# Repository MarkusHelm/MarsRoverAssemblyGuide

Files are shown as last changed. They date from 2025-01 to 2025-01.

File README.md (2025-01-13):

# Mechanical

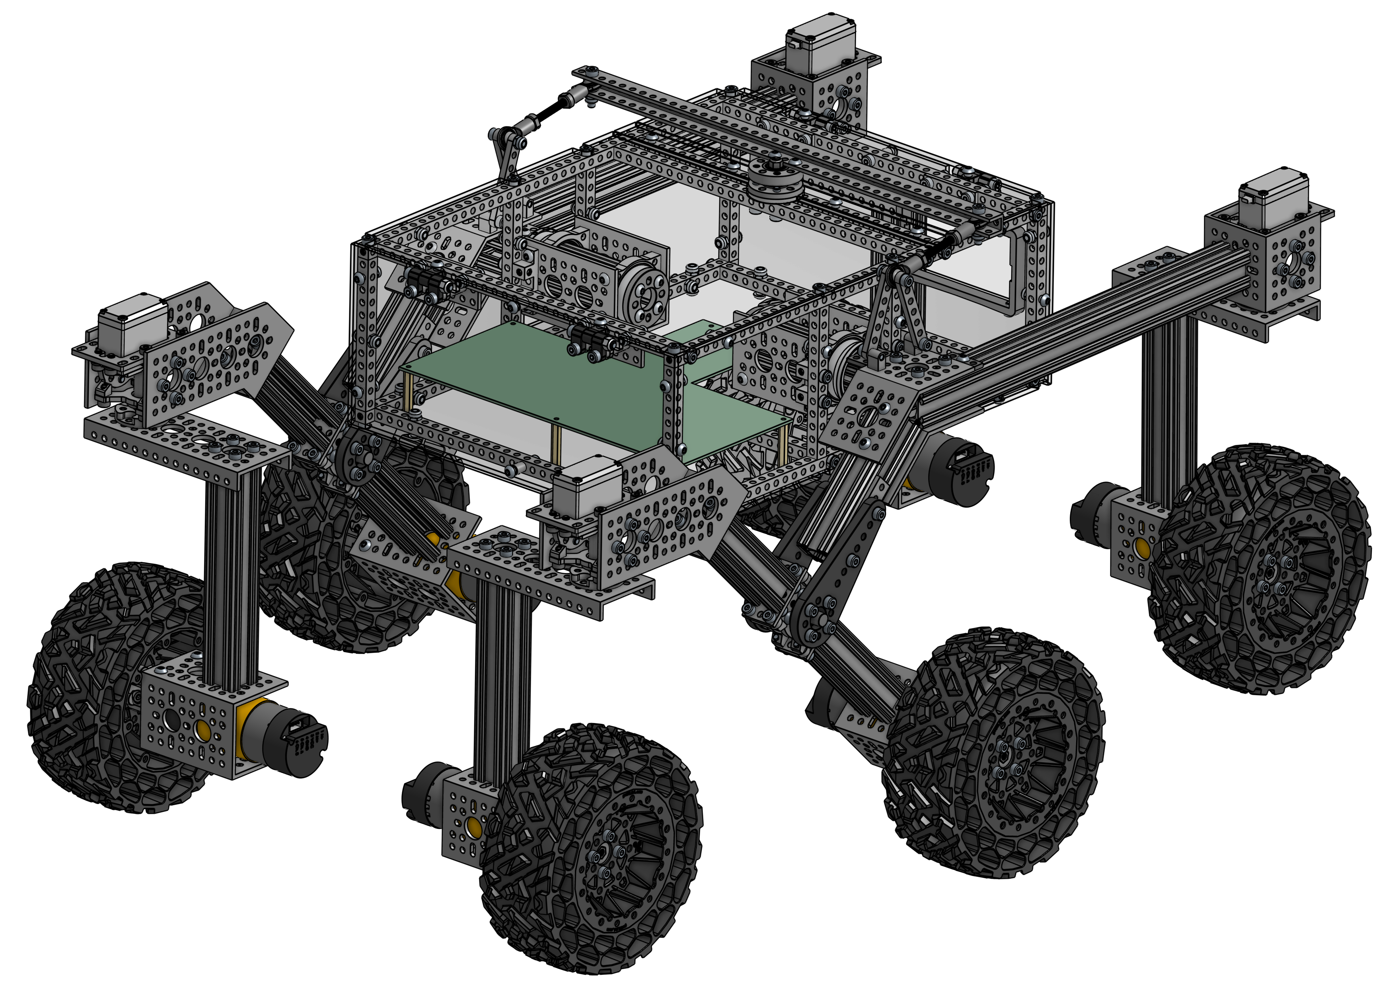
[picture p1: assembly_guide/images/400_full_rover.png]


## Assembly Guide

👉 [`Mechanical Assembly Guide`](./assembly_guide/readme.md)

## Required Parts

This is a summary of all the mechanical parts you need to build the rover. The amount is always the number of the `individual parts`. Some parts are sold in `(packs)`. The number in brackets indicates, how many packs you need.

> ⚠️ Be very careful when ordering the parts! Many parts have multiple variants, some with very small differences. It is important that you get the exact parts listed!

#### goBILDA Parts

| Amount | Part | Part Number | Link | Chapter |
| :----: | --- | --- | --- | --- |
| 1 | 1101 Series U-Beam (**41 Hole**, 328mm Length) | 1101-0041-0328 | https://www.gobilda.com/1101-series-u-beam-41-hole-328mm-length/ | Main Body |
| 8 (4)  | 1102 Series Flat Beam (**3 Hole**, 24mm Length) - 2 Pack | 1102-0003-0024 | https://www.gobilda.com/1102-series-flat-beam-3-hole-24mm-length-2-pack/ | Rocker Bogie |
| 4 (2)  | 1102 Series Flat Beam (**7 Hole**, 56mm Length) - 2 Pack | 1102-0007-0056 | https://www.gobilda.com/1102-series-flat-beam-7-hole-56mm-length-2-pack/ | Rocker Bogie |
| 8 | 1106 Series Square Beam (**12 Hole**, 96mm Length) | 1106-0012-0096 | https://www.gobilda.com/1106-series-square-beam-12-hole-96mm-length/ | Main Body |
| 7 | 1106 Series Square Beam (**29 Hole**, 232mm Length) | 1106-0029-0232 | https://www.gobilda.com/1106-series-square-beam-29-hole-232mm-length/ | Main Body |
| 4 | 1106 Series Square Beam (**41 Hole**, 328mm Length) | 1106-0041-0328 | https://www.gobilda.com/1106-series-square-beam-41-hole-328mm-length/ | Main Body |
| 4 | 1109 Series goRAIL (**144mm Length**) | 1109-0024-0144 | https://www.gobilda.com/1109-series-gorail-144mm-length/ | Wheels |
| 4 | 1111 Series Angle Pattern Bracket (**1-1**) | 1111-0001-0001 | https://www.gobilda.com/1111-series-angle-pattern-bracket-1-1/ | Rocker Bogie |
| 2 | 1111 Series Angle Pattern Bracket (**3-1**) | 1111-0003-0001 | https://www.gobilda.com/1111-series-angle-pattern-bracket-3-1/ | Rocker Bogie |
| 4 (2)  | 1114 Series Flat Bracket (**1-1**) - 2 Pack | 1114-0001-0001 | https://www.gobilda.com/1114-series-flat-bracket-1-1-2-pack/ | Rocker Bogie |
| 8 | 1116 Series Grid Plate (**3 x 5 Hole**, 24 x 40mm) | 1116-0024-0040 | https://www.gobilda.com/1116-series-grid-plate-3-x-5-hole-24-x-40mm/ | Main Body, Wheels, Rocker Bogie |
| 6 | 1118 Series Open goRAIL (**96mm Length**) | 1118-0024-0096 | https://www.gobilda.com/1118-series-open-gorail-96mm-length/ | Wheels, Rocker Bogie |
| 2 | 1118 Series Open goRAIL (**120mm Length**) | 1118-0024-0120 | https://www.gobilda.com/1118-series-open-gorail-120mm-length/ | Rocker Bogie |
| 2 | 1118 Series Open goRAIL (**288mm Length**) | 1118-0024-0288 | https://www.gobilda.com/1118-series-open-gorail-288mm-length/ | Rocker Bogie |
| 2 | 1120 Series U-Channel (**1 Hole**, 48mm Length) | 1120-0001-0048 | https://www.gobilda.com/1120-series-u-channel-1-hole-48mm-length/ | Rocker Bogie |
| 8 | 1120 Series U-Channel (**2 Hole**, 72mm Length) | 1120-0002-0072 | https://www.gobilda.com/1120-series-u-channel-2-hole-72mm-length/ | Main Body, Wheels |
| 4 | 1121 Series Low-Side U-Channel (**4 Hole**, 120mm Length) | 1121-0004-0120 | https://www.gobilda.com/1121-series-low-side-u-channel-4-hole-120mm-length/ | Wheels |
| 2 (1)  | 1137 Series Steel Flat Grid Bracket (1-1) - 2 Pack | 1137-0001-0001 | https://www.gobilda.com/1137-series-steel-flat-grid-bracket-1-1-2-pack/ | Rocker Bogie |
| 4 (1)  | 1203 Series Block Mount (1-1) - 4 Pack | 1203-0001-0001 | https://www.gobilda.com/1203-series-block-mount-1-1-4-pack/ | Rocker Bogie |
| 4 (2)  | 1205 Series Dual Block Mount (1-4) - 2 Pack | 1205-0001-0004 | https://www.gobilda.com/1205-series-dual-block-mount-1-4-2-pack/ | Main Body |
| 4 | 1221 Series 2-Side, 2-Post Pattern Mount (**32-2**) | 1221-0032-0002 | https://www.gobilda.com/1221-series-2-side-2-post-pattern-mount-32-2/ | Rocker Bogie |
| 2 | 1309 Series Sonic Hub (**8mm Bore**) | 1309-0016-0008 | https://www.gobilda.com/1309-series-sonic-hub-8mm-bore/ | Rocker Bogie |
| 6 | 1310 Series Hyper Hub (**8mm REX™** Bore) | 1310-0016-4008 | https://www.gobilda.com/1310-series-hyper-hub-8mm-rex-bore/ | Wheels |
| 6 | 1401 Series 2-Side, 2-Post Clamping Mount (**43mm Width**, **36mm Bore**) | 1401-0043-0036 | https://www.gobilda.com/1401-series-2-side-2-post-clamping-mount-43mm-width-36mm-bore/ | Wheels |
| 4 (1)  | 1501 Series M4 x 0.7mm Standoff (**6mm OD**, **8mm Length**) - 4 Pack | 1501-0006-0080 | https://www.gobilda.com/1501-series-m4-x-0-7mm-standoff-6mm-od-8mm-length-4-pack/ | Main Body |
| 8 (2)  | 1501 Series M4 x 0.7mm Standoff (**6mm OD**, **22mm Length**) - 4 Pack | 1501-0006-0220 | https://www.gobilda.com/1501-series-m4-x-0-7mm-standoff-6mm-od-22mm-length-4-pack/ | Main Body |
| 4 | 1504 Series **32mm OD** Pattern Spacer (**2mm Length**) | 1504-0032-0020 | https://www.gobilda.com/1504-series-32mm-od-pattern-spacer-2mm-length/ | Rocker Bogie |
| 6 (3)  | 1506 Series 32mm ID Spacer (36mm OD, **6mm Length**) - 2 Pack | 1506-0032-0006 | https://www.gobilda.com/1506-series-32mm-id-spacer-36mm-od-6mm-length-2-pack/ | Rocker Bogie, Final Steps |
| 2 (1)  | goTUBE Endcap (14mm Bore, 36mm OD, 4mm Thick) - 4 Pack | 1519-0014-0400 | https://www.gobilda.com/gotube-endcap-14mm-bore-36mm-od-4mm-thick-4-pack/ | Final Steps |
| 2 (1)  | 1522 Series 8mm ID Spacer (10mm OD, **4mm Length**) - 4 Pack | 1522-0010-0040 | https://www.gobilda.com/1522-series-8mm-id-spacer-10mm-od-4mm-length-4-pack/ | Rocker Bogie |
| 2 (1)  | 1522 Series 8mm ID Spacer (10mm OD, **6mm Length**) - 4 Pack | 1522-0010-0060 | https://www.gobilda.com/1522-series-8mm-id-spacer-10mm-od-6mm-length-4-pack/ | Rocker Bogie |
| 4 | **32mm** Bore 2-Side, 2-Post Pillow Block (**43mm Width**) | 1604-0043-0032 | https://www.gobilda.com/32mm-bore-2-side-2-post-pillow-block-43mm-width/ | Main Body |
| 1 | Idler Bearing-Hub (**32mm OD**, **16mm Height**) | 1608-0001-0001 | https://www.gobilda.com/idler-bearing-hub-32mm-od-16mm-height/ | Main Body |
| 4 (2)  | 1611 Series Flanged Ball Bearing (**8mm ID** x **14mm OD**, **5mm Thickness**) - 2 Pack | 1611-0514-0008 | https://www.gobilda.com/1611-series-flanged-ball-bearing-8mm-id-x-14mm-od-5mm-thickness-2-pack/ | Rocker Bogie |
| 4 | Plastic Hub-Mount Control Arm (**72mm Length**) | 1916-0014-0072 | https://www.gobilda.com/plastic-hub-mount-control-arm-72mm-length/ | Rocker Bogie |
| 4 | 2000 Series Dual Mode Servo (**25-2**, **Torque**) | 2000-0025-0002 | https://www.gobilda.com/2000-series-dual-mode-servo-25-2-torque/ | Rocker Bogie |
| 2 | **8mm** Shaft (Stainless Steel, **50mm Length**) | 2100-0008-0050 | https://www.gobilda.com/8mm-shaft-stainless-steel-50mm-length/ | Rocker Bogie |
| 32 (2) | Hurricane Nut for goRAIL - 25 Pack | 2805-0004-0108 | https://www.gobilda.com/hurricane-nut-for-gorail-25-pack/ | Rocker Bogie |
| 2 (1)  | 2808 Series Stainless Steel Threaded Rod (M4 x 0.7mm, **50mm Length**) - 2 Pack | 2808-0004-0050 | https://www.gobilda.com/2808-series-stainless-steel-threaded-rod-m4-x-0-7mm-50mm-length-2-pack/ | Rocker Bogie |
| 4 (2)  | Plastic Hinge - 2 Pack | 2902-0003-0001 | https://www.gobilda.com/plastic-hinge-2-pack/ | Main Body |
| 4 (2)  | 2913 Series Steel Ball Linkage (**Female** M4 x 0.7mm, 24.1mm Length) - 2 Pack | 2913-0004-0241 | https://www.gobilda.com/2913-series-steel-ball-linkage-female-m4-x-0-7mm-24-1mm-length-2-pack/ | Rocker Bogie |
| 4 | ServoBlock® (Standard Size, 25 Tooth Spline, Hub-Shaft) | 3202-0001-2501 | https://www.gobilda.com/servoblock-standard-size-25-tooth-spline-hub-shaft/ | Rocker Bogie |
| 6 | Wasteland Wheel (**144mm Diameter**, **52mm Width**) | 3616-0014-0144 | https://www.gobilda.com/wasteland-wheel-144mm-diameter-52mm-width/ | Wheels |
| 6 | 5203 Series Yellow Jacket Planetary Gear Motor (26.9:1 Ratio, **24mm Length** **8mm REX™** Shaft, **223 RPM**, 3.3 - 5V Encoder) | 5203-2402-0027 | https://www.gobilda.com/5203-series-yellow-jacket-planetary-gear-motor-26-9-1-ratio-24mm-length-8mm-rex-shaft-223-rpm-3-3-5v-encoder/ | Wheels |
| 55 (3) | `M4` x 0.7mm Nylock Nut - 25 Pack | 2812-0004-0007 | https://www.gobilda.com/m4-x-0-7mm-nylock-nut/?sku=2812-0004-0007 | |

#### Generic Parts

| Amount | Part |
| :----: | --- |
| 72 | `M4 x 6mm` Button Head Screw  |
| 44 | `M4 x 10mm` Button Head Screw |
| 39 | `M4 x 16mm` Button Head Screw |
| 74 | `M4 x 8mm` Socket Head Screw  |
|  120 | `M4 x 12mm` Socket Head Screw |
| 50 | `M4 x 16mm` Socket Head Screw |
| 4 | `M4 x 20mm` Socket Head Screw |
| 32 | `M4 x 0.1mm` Washer |

#### Lasercut Parts

| Amount | Part | File |
| :----: | --- | --- |
| 1 | Bottom Plate | [bottom_plate.dxf](./laser_cut_parts/bottom_plate.dxf) |
| 2 | Side Plate | [side_plate.dxf](./laser_cut_parts/side_plate.dxf) |
| 1 | Front Plate | [front_plate.dxf](./laser_cut_parts/front_plate.dxf) |
| 1 | Back Plate | [back_plate.dxf](./laser_cut_parts/back_plate.dxf) |
| 1 | Top Plate Front | [top_plate_front.dxf](./laser_cut_parts/top_plate_front.dxf) |
| 1 | Top Plate Gap | [top_plate_gap.dxf](./laser_cut_parts/top_plate_gap.dxf) |
| 1 | Top Plate Back  | [top_plate_back.dxf](./laser_cut_parts/top_plate_back.dxf) |

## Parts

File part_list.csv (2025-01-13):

SKU | Part | Part Qty. | Pack Size | Pack Qty. | URL | Assembly
1101-0041-0328 | 1101 Series U-Beam (41 Hole, 328mm Length) | 1 | 1 | 1 | https://www.gobilda.com/1101-series-u-beam-41-hole-328mm-length/ | Main Body
1102-0003-0024 | 1102 Series Flat Beam (3 Hole, 24mm Length) - 2 Pack | 8 | 2 | 4 | https://www.gobilda.com/1102-series-flat-beam-3-hole-24mm-length-2-pack/ | Rocker Bogie
1102-0007-0056 | 1102 Series Flat Beam (7 Hole, 56mm Length) - 2 Pack | 4 | 2 | 2 | https://www.gobilda.com/1102-series-flat-beam-7-hole-56mm-length-2-pack/ | Rocker Bogie
1106-0012-0096 | 1106 Series Square Beam (12 Hole, 96mm Length) | 8 | 1 | 8 | https://www.gobilda.com/1106-series-square-beam-12-hole-96mm-length/ | Main Body
1106-0029-0232 | 1106 Series Square Beam (29 Hole, 232mm Length) | 7 | 1 | 7 | https://www.gobilda.com/1106-series-square-beam-29-hole-232mm-length/ | Main Body
1106-0041-0328 | 1106 Series Square Beam (41 Hole, 328mm Length) | 4 | 1 | 4 | https://www.gobilda.com/1106-series-square-beam-41-hole-328mm-length/ | Main Body
1109-0024-0144 | 1109 Series goRAIL (144mm Length) | 4 | 1 | 4 | https://www.gobilda.com/1109-series-gorail-144mm-length/ | Wheels
1111-0001-0001 | 1111 Series Angle Pattern Bracket (1-1) | 4 | 1 | 4 | https://www.gobilda.com/1111-series-angle-pattern-bracket-1-1/ | Rocker Bogie
1111-0003-0001 | 1111 Series Angle Pattern Bracket (3-1) | 2 | 1 | 2 | https://www.gobilda.com/1111-series-angle-pattern-bracket-3-1/ | Rocker Bogie
1114-0001-0001 | 1114 Series Flat Bracket (1-1) - 2 Pack | 4 | 2 | 2 | https://www.gobilda.com/1114-series-flat-bracket-1-1-2-pack/ | Rocker Bogie
1116-0024-0040 | 1116 Series Grid Plate (3 x 5 Hole, 24 x 40mm) | 8 | 1 | 8 | https://www.gobilda.com/1116-series-grid-plate-3-x-5-hole-24-x-40mm/ | Main Body, Wheels, Rocker Bogie
1118-0024-0096 | 1118 Series Open goRAIL (96mm Length) | 6 | 1 | 6 | https://www.gobilda.com/1118-series-open-gorail-96mm-length/ | Wheels, Rocker Bogie
1118-0024-0120 | 1118 Series Open goRAIL (120mm Length) | 2 | 1 | 2 | https://www.gobilda.com/1118-series-open-gorail-120mm-length/ | Rocker Bogie
1118-0024-0288 | 1118 Series Open goRAIL (288mm Length) | 2 | 1 | 2 | https://www.gobilda.com/1118-series-open-gorail-288mm-length/ | Rocker Bogie
1120-0001-0048 | 1120 Series U-Channel (1 Hole, 48mm Length) | 2 | 1 | 2 | https://www.gobilda.com/1120-series-u-channel-1-hole-48mm-length/ | Rocker Bogie
1120-0002-0072 | 1120 Series U-Channel (2 Hole, 72mm Length) | 8 | 1 | 8 | https://www.gobilda.com/1120-series-u-channel-2-hole-72mm-length/ | Main Body, Wheels
1121-0004-0120 | 1121 Series Low-Side U-Channel (4 Hole, 120mm Length) | 4 | 1 | 4 | https://www.gobilda.com/1121-series-low-side-u-channel-4-hole-120mm-length/ | Wheels
1137-0001-0001 | 1137 Series Steel Flat Grid Bracket (1-1) - 2 Pack | 2 | 2 | 1 | https://www.gobilda.com/1137-series-steel-flat-grid-bracket-1-1-2-pack/ | Rocker Bogie
1203-0001-0001 | 1203 Series Block Mount (1-1) - 4 Pack | 4 | 4 | 1 | https://www.gobilda.com/1203-series-block-mount-1-1-4-pack/ | Rocker Bogie
1205-0001-0004 | 1205 Series Dual Block Mount (1-4) - 2 Pack | 4 | 2 | 2 | https://www.gobilda.com/1205-series-dual-block-mount-1-4-2-pack/ | Main Body
1221-0032-0002 | 1221 Series 2-Side, 2-Post Pattern Mount (32-2) | 4 | 1 | 4 | https://www.gobilda.com/1221-series-2-side-2-post-pattern-mount-32-2/ | Rocker Bogie
1309-0016-0008 | 1309 Series Sonic Hub (8mm Bore) | 2 | 1 | 2 | https://www.gobilda.com/1309-series-sonic-hub-8mm-bore/ | Rocker Bogie
1310-0016-4008 | 1310 Series Hyper Hub (8mm REX™ Bore) | 6 | 1 | 6 | https://www.gobilda.com/1310-series-hyper-hub-8mm-rex-bore/ | Wheels
1401-0043-0036 | 1401 Series 2-Side, 2-Post Clamping Mount (43mm Width, 36mm Bore) | 6 | 1 | 6 | https://www.gobilda.com/1401-series-2-side-2-post-clamping-mount-43mm-width-36mm-bore/ | Wheels
1501-0006-0080 | 1501 Series M4 x 0.7mm Standoff (6mm OD, 8mm Length) - 4 Pack | 4 | 4 | 1 | https://www.gobilda.com/1501-series-m4-x-0-7mm-standoff-6mm-od-8mm-length-4-pack/ | Main Body
1501-0006-0220 | 1501 Series M4 x 0.7mm Standoff (6mm OD, 22mm Length) - 4 Pack | 8 | 4 | 2 | https://www.gobilda.com/1501-series-m4-x-0-7mm-standoff-6mm-od-22mm-length-4-pack/ | Main Body
1504-0032-0020 | 1504 Series 32mm OD Pattern Spacer (2mm Length) | 4 | 1 | 4 | https://www.gobilda.com/1504-series-32mm-od-pattern-spacer-2mm-length/ | Rocker Bogie
1506-0032-0006 | 1506 Series 32mm ID Spacer (36mm OD, 6mm Length) - 2 Pack | 6 | 2 | 3 | https://www.gobilda.com/1506-series-32mm-id-spacer-36mm-od-6mm-length-2-pack/ | Rocker Bogie, Final Steps
1519-0014-0400 | goTUBE Endcap (14mm Bore, 36mm OD, 4mm Thick) - 4 Pack | 2 | 4 | 1 | https://www.gobilda.com/gotube-endcap-14mm-bore-36mm-od-4mm-thick-4-pack/ | Final Steps
1522-0010-0040 | 1522 Series 8mm ID Spacer (10mm OD, 4mm Length) - 4 Pack | 2 | 4 | 1 | https://www.gobilda.com/1522-series-8mm-id-spacer-10mm-od-4mm-length-4-pack/ | Rocker Bogie
1522-0010-0060 | 1522 Series 8mm ID Spacer (10mm OD, 6mm Length) - 4 Pack | 2 | 4 | 1 | https://www.gobilda.com/1522-series-8mm-id-spacer-10mm-od-6mm-length-4-pack/ | Rocker Bogie
1604-0043-0032 | 32mm Bore 2-Side, 2-Post Pillow Block (43mm Width) | 4 | 1 | 4 | https://www.gobilda.com/32mm-bore-2-side-2-post-pillow-block-43mm-width/ | Main Body
1608-0001-0001 | Idler Bearing-Hub (32mm OD, 16mm Height) | 1 | 1 | 1 | https://www.gobilda.com/idler-bearing-hub-32mm-od-16mm-height/ | Main Body
1611-0514-0008 | 1611 Series Flanged Ball Bearing (8mm ID x 14mm OD, 5mm Thickness) - 2 Pack | 4 | 2 | 2 | https://www.gobilda.com/1611-series-flanged-ball-bearing-8mm-id-x-14mm-od-5mm-thickness-2-pack/ | Rocker Bogie
1916-0014-0072 | Plastic Hub-Mount Control Arm (72mm Length) | 4 | 1 | 4 | https://www.gobilda.com/plastic-hub-mount-control-arm-72mm-length/ | Rocker Bogie
2000-0025-0002 | 2000 Series Dual Mode Servo (25-2, Torque) | 4 | 1 | 4 | https://www.gobilda.com/2000-series-dual-mode-servo-25-2-torque/ | Rocker Bogie
2100-0008-0050 | 8mm Shaft (Stainless Steel, 50mm Length) | 2 | 1 | 2 | https://www.gobilda.com/8mm-shaft-stainless-steel-50mm-length/ | Rocker Bogie
2805-0004-0108 | Hurricane Nut for goRAIL - 25 Pack | 32 | 25 | 2 | https://www.gobilda.com/hurricane-nut-for-gorail-25-pack/ | Rocker Bogie
2808-0004-0050 | 2808 Series Stainless Steel Threaded Rod (M4 x 0.7mm, 50mm Length) - 2 Pack | 2 | 2 | 1 | https://www.gobilda.com/2808-series-stainless-steel-threaded-rod-m4-x-0-7mm-50mm-length-2-pack/ | Rocker Bogie
2902-0003-0001 | Plastic Hinge - 2 Pack | 4 | 2 | 2 | https://www.gobilda.com/plastic-hinge-2-pack/ | Main Body
2913-0004-0241 | 2913 Series Steel Ball Linkage (Female M4 x 0.7mm, 24.1mm Length) - 2 Pack | 4 | 2 | 2 | https://www.gobilda.com/2913-series-steel-ball-linkage-female-m4-x-0-7mm-24-1mm-length-2-pack/ | Rocker Bogie
3202-0001-2501 | ServoBlock® (Standard Size, 25 Tooth Spline, Hub-Shaft) | 4 | 1 | 4 | https://www.gobilda.com/servoblock-standard-size-25-tooth-spline-hub-shaft/ | Rocker Bogie
3616-0014-0144 | Wasteland Wheel (144mm Diameter, 52mm Width) | 6 | 1 | 6 | https://www.gobilda.com/wasteland-wheel-144mm-diameter-52mm-width/ | Wheels
5203-2402-0027 | 5203 Series Yellow Jacket Planetary Gear Motor (26.9:1 Ratio, 24mm Length 8mm REX™ Shaft, 223 RPM, 3.3 - 5V Encoder) | 6 | 1 | 6 | https://www.gobilda.com/5203-series-yellow-jacket-planetary-gear-motor-26-9-1-ratio-24mm-length-8mm-rex-shaft-223-rpm-3-3-5v-encoder/ | Wheels
2812-0004-0007 | `M4` x 0.7mm Nylock Nut - 25 Pack | 55 | 25 | 3 | https://www.gobilda.com/m4-x-0-7mm-nylock-nut/?sku=2812-0004-0007 | Generic
 | `M4 x 6mm` Button Head Screw | 72 |  |  |  | Generic
 | `M4 x 10mm` Button Head Screw | 44 |  |  |  | Generic
 | `M4 x 16mm` Button Head Screw | 39 |  |  |  | Generic
 | `M4 x 8mm` Socket Head Screw | 74 |  |  |  | Generic
 | `M4 x 12mm` Socket Head Screw | 120 |  |  |  | Generic
 | `M4 x 16mm` Socket Head Screw | 50 |  |  |  | Generic
 | `M4 x 20mm` Socket Head Screw | 4 |  |  |  | Generic
 | `M4 x 0.1mm` Washer | 32 |  |  |  | Generic

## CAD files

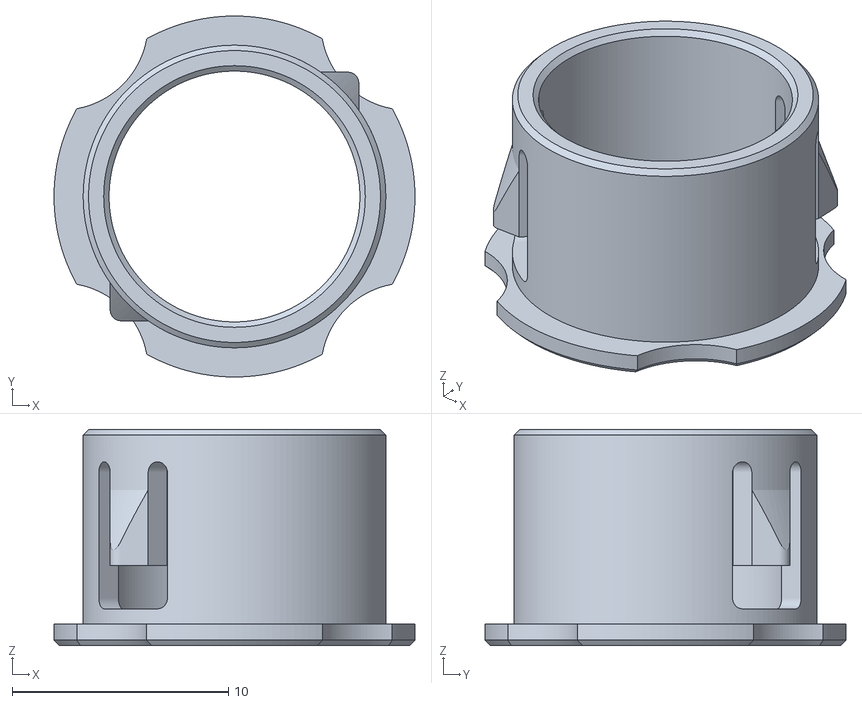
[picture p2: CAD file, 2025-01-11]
3d_printable_parts/plastic_grommet.stl
16.7 x 16.7 x 10.0

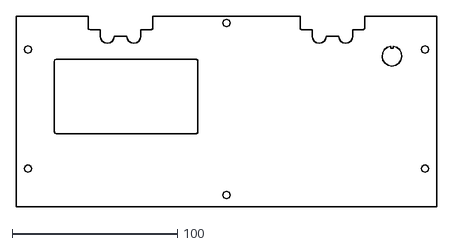
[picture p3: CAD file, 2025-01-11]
laser_cut_parts/back_plate.dxf
254.0 x 115.0

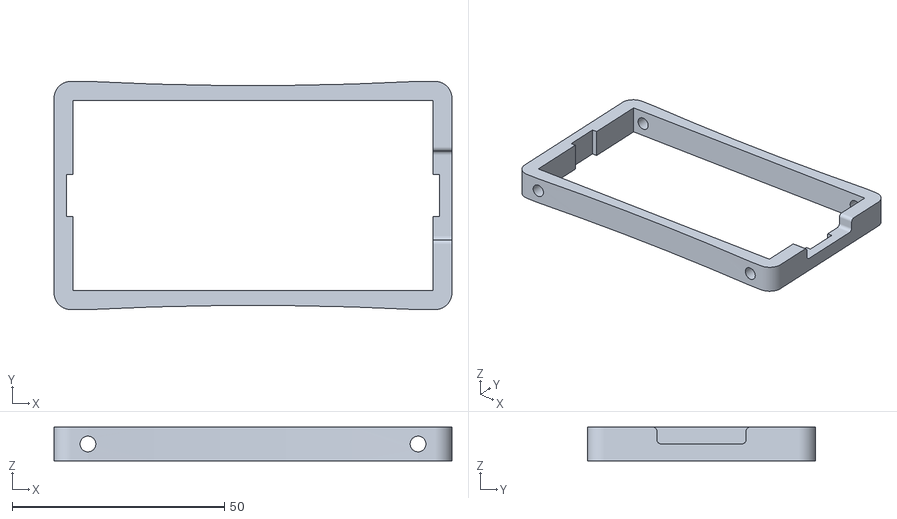
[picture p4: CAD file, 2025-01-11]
3d_printable_parts/multimeter_mount.stl
93.8 x 53.8 x 8.00

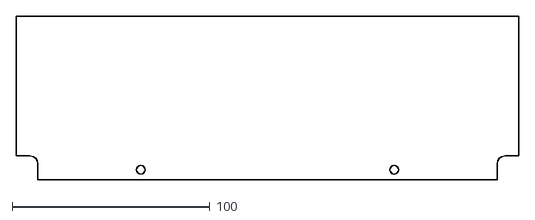
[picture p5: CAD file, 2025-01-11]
laser_cut_parts/top_plate_back.dxf
254.0 x 82.5

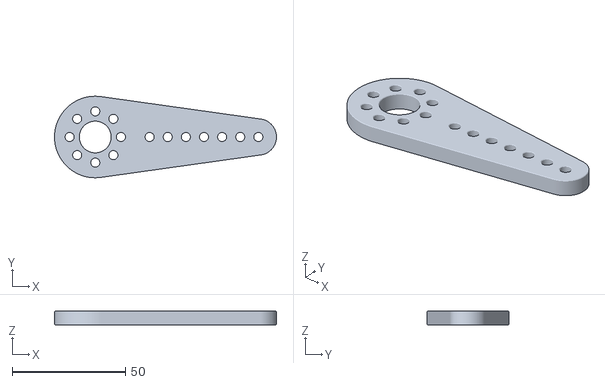
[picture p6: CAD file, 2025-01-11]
3d_printable_parts/plastic_control_arm.stl
98.0 x 36.0 x 6.00

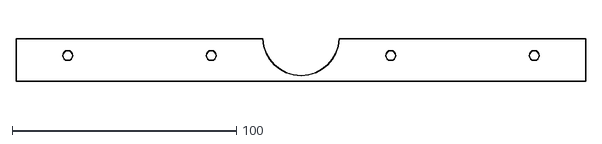
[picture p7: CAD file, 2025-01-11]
laser_cut_parts/top_plate_gap.dxf
254.0 x 19.0

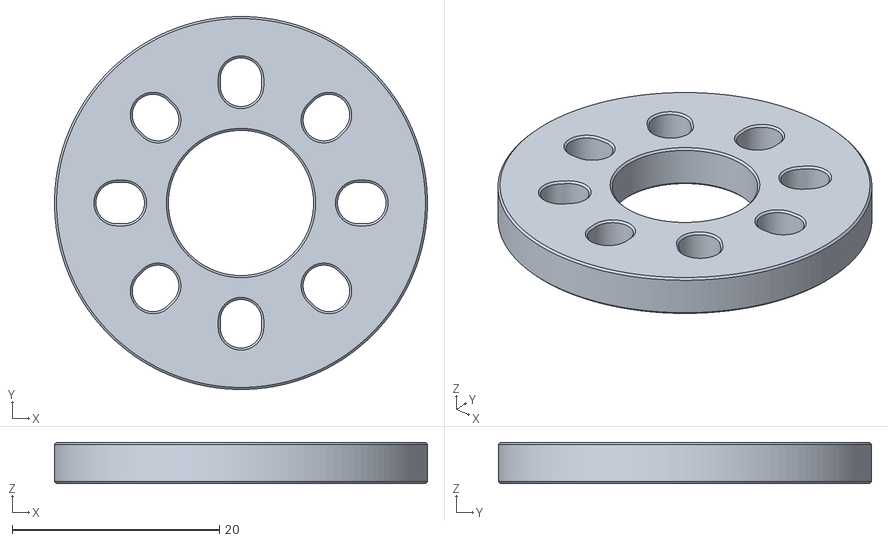
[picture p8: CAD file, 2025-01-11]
3d_printable_parts/gotube_endcap.stl
36.0 x 36.0 x 4.00

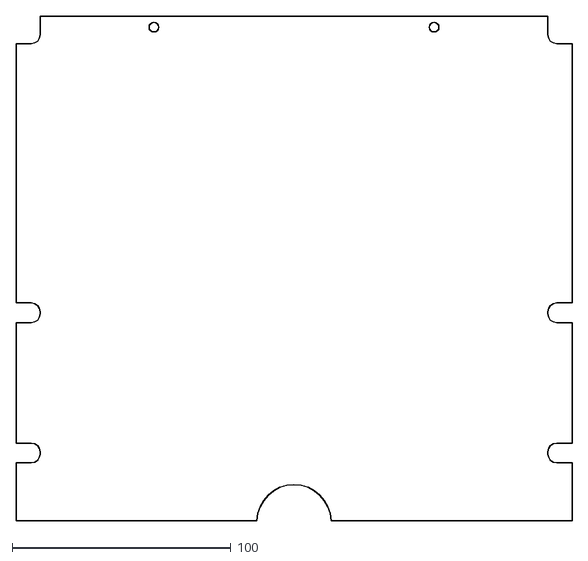
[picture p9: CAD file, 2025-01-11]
laser_cut_parts/top_plate_front.dxf
254.0 x 230.5

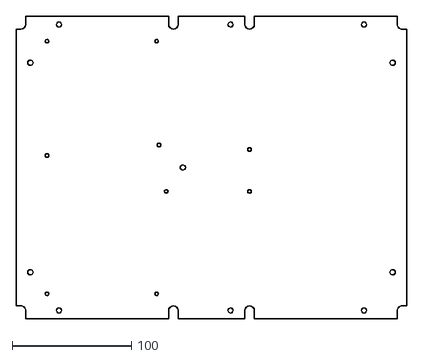
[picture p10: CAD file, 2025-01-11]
laser_cut_parts/bottom_plate.dxf
328.0 x 254.0

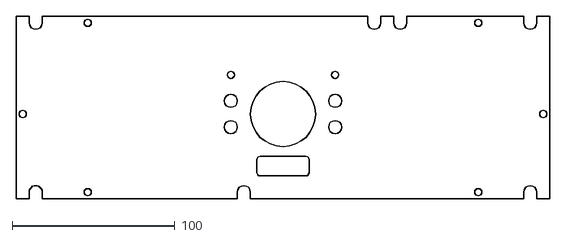
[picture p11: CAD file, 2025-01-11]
laser_cut_parts/side_plate.dxf
328.0 x 112.0

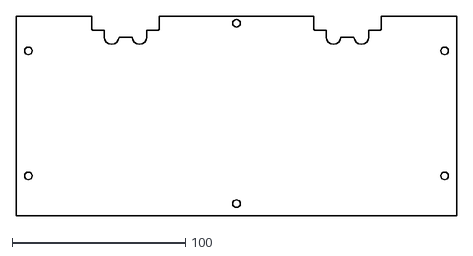
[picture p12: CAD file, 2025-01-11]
laser_cut_parts/front_plate.dxf
254.0 x 115.0

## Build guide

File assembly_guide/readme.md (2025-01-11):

# Assembly Guide

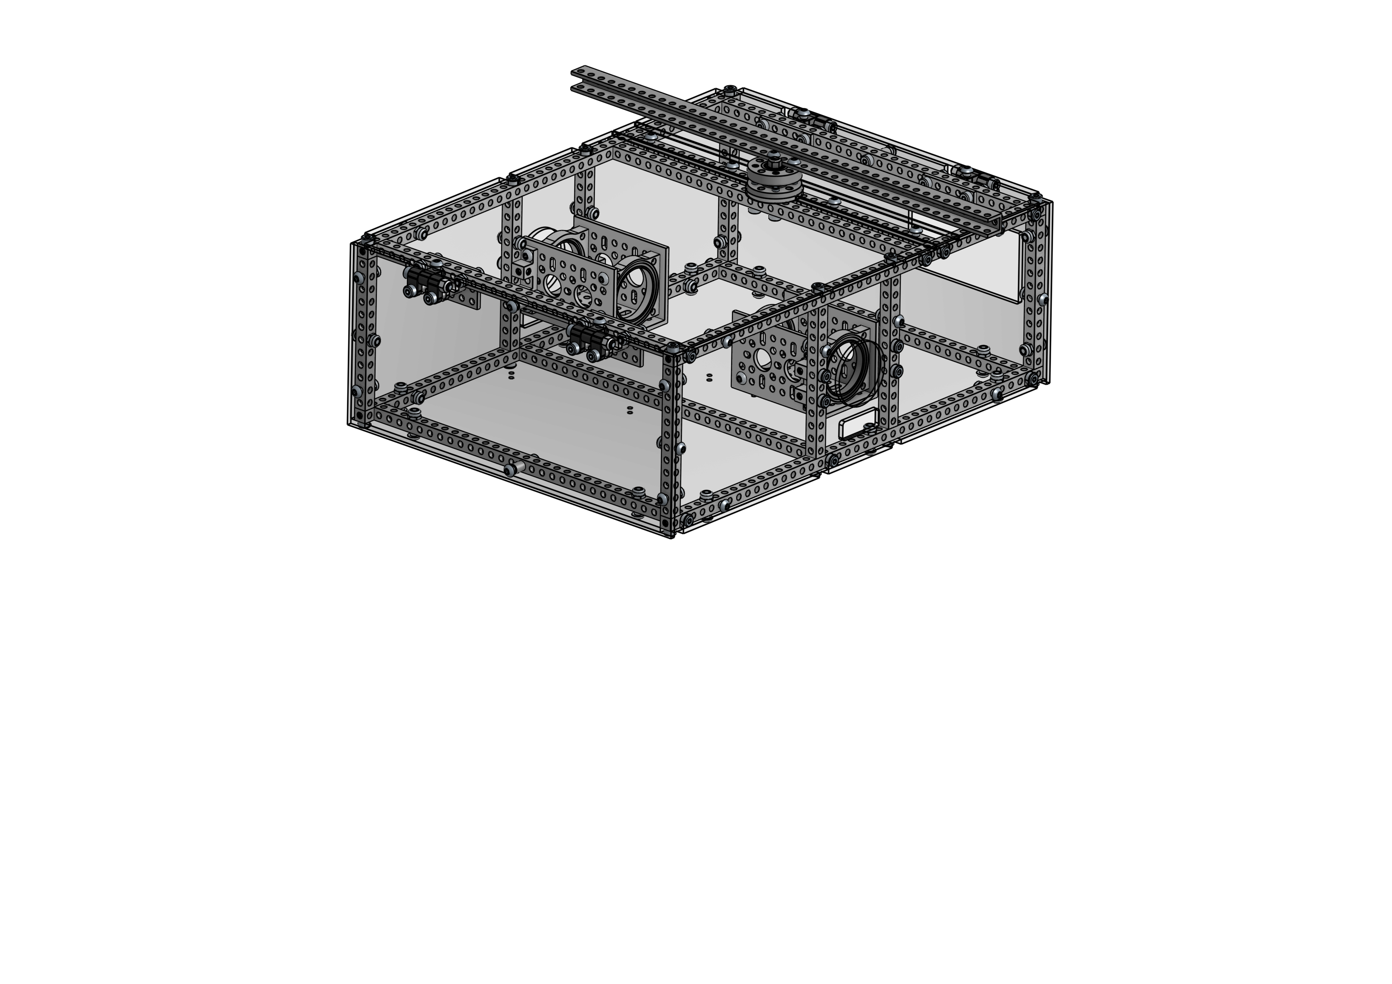
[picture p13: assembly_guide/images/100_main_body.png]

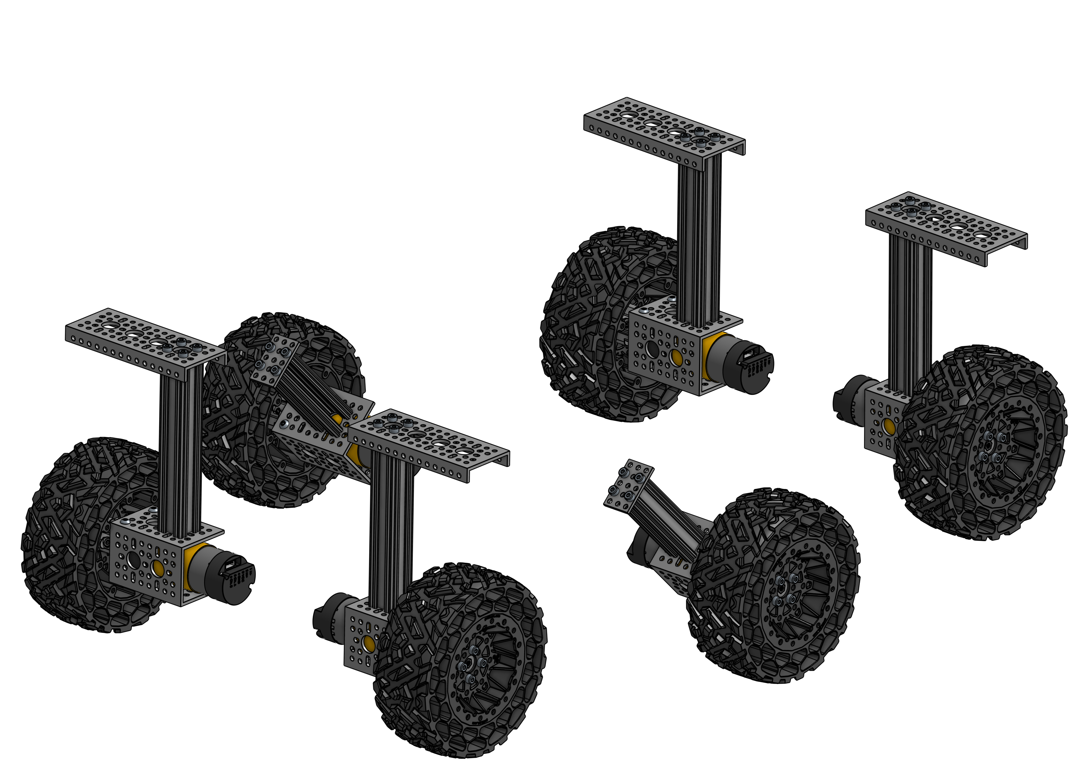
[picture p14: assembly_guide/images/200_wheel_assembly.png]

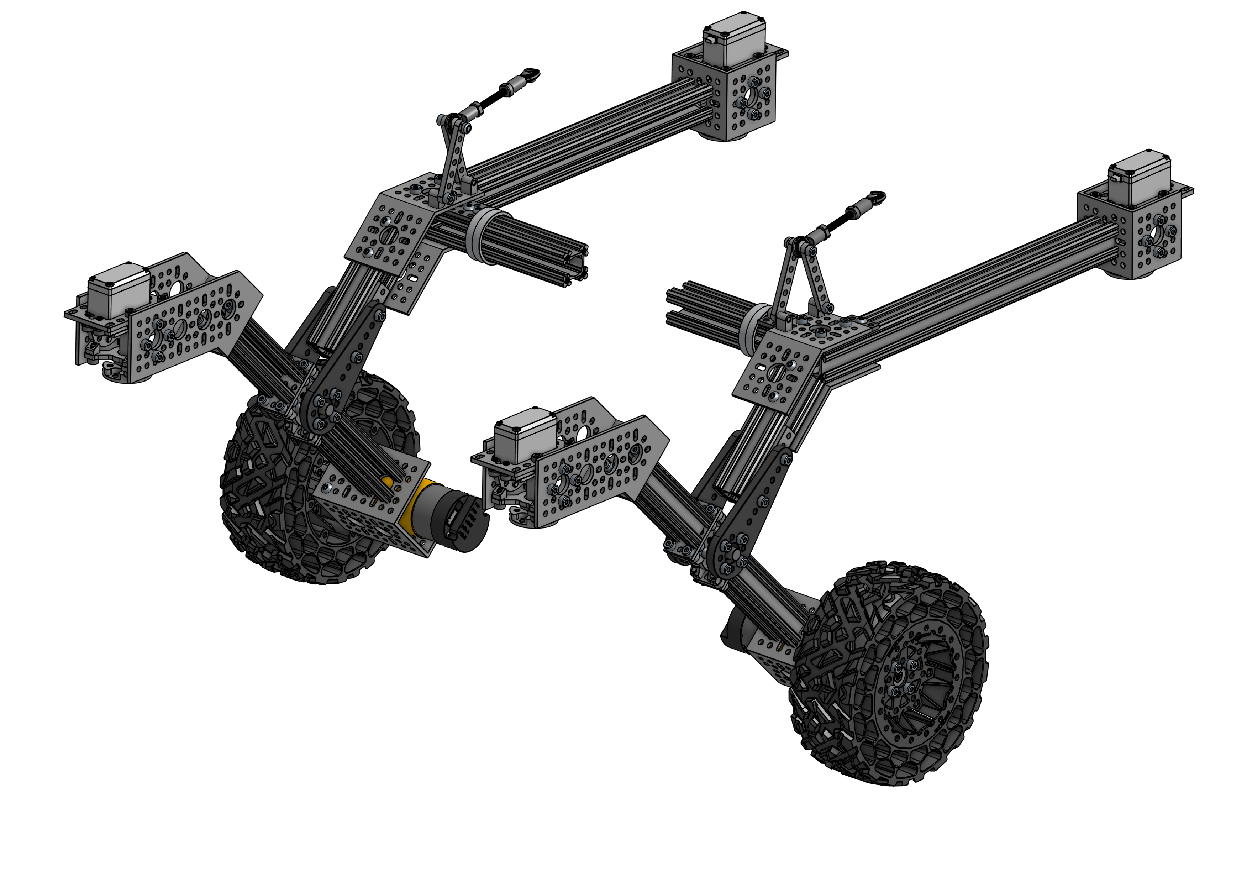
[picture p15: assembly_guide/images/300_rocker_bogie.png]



This guide covers all the mechanical steps to build your own little mars rover. The assembly is divided into four chapters to give you a better overview of what needs to be done. Each chapter consists of several assembly steps, each with its own parts list and assembly instructions. You can follow this guide step by step and have your parts ready when you need them.

1. [Main Body](1_main_body.md#1-main-body)
   - 1.1 [Aluminum Frame](1_main_body.md#11-aluminum-frame) `👈 Start here`
   - 1.2 [Wall Standoffs](1_main_body.md#12-wall-standoffs)
   - 1.3 [Axis Clamps (2x)](1_main_body.md#13-axis-clamps-2x)
   - 1.4 [Axis Clamp Installation](1_main_body.md#14-axis-clamp-installation)
   - 1.5 [Top Plate Hinges (4x)](1_main_body.md#15-top-plate-hinges-4x)
   - 1.6 [Top Plate Hinge Installation](1_main_body.md#16-top-plate-hinge-installation)
   - 1.7 [Bottom Plate](1_main_body.md#17-bottom-plate)
   - 1.8 [Side Plates](1_main_body.md#18-side-plates)
   - 1.9 [Front and Back Plates](1_main_body.md#19-front-and-back-plates)
   - 1.10 [Top Plates](1_main_body.md#110-top-plates)
   - 1.11 [Differential Pivot](1_main_body.md#111-differential-pivot)
2. [Wheels](2_wheels.md#2-wheels)
   - 2.1 [Corner Wheels (2L/2R)](2_wheels.md#21-corner-wheels-2l2r)
   - 2.2 [Middle Wheels (L/R)](2_wheels.md#22-middle-wheels-lr)
3. [Rocker Bogie](3_rocker_bogie.md#3-rocker-bogie)
   - 3.1 [Hinge Outer Part (4x)](3_rocker_bogie.md#31-hinge-outer-part-4x)
   - 3.2 [Hinge Inner Part (2x)](3_rocker_bogie.md#32-hinge-inner-part-2x)
   - 3.3 [Hinge Assembly (2x)](3_rocker_bogie.md#33-hinge-assembly-2x)
   - 3.4 [Servo Block (4x)](3_rocker_bogie.md#34-servo-block-4x)
   - 3.5 [Rear Servo Arm (L/R)](3_rocker_bogie.md#35-rear-servo-arm-lr)
   - 3.6 [Front Servo Arm (L/R)](3_rocker_bogie.md#36-front-servo-arm-lr)
   - 3.7 [Pivot Plate (L/R)](3_rocker_bogie.md#37-pivot-plate-lr)
   - 3.8 [Top Plate (L/R)](3_rocker_bogie.md#38-top-plate-lr)
   - 3.9 [Rocker Bogie Rear Assembly (L/R)](3_rocker_bogie.md#39-rocker-bogie-rear-assembly-lr)
   - 3.10 [Rocker Bogie Front Assembly (L/R)](3_rocker_bogie.md#310-rocker-bogie-front-assembly-lr)
4. [Final Steps](4_final_steps.md#4-final-steps)
   - 4.1 [Rocker Bogie Insertion](4_final_steps.md#41-rocker-bogie-insertion)
   - 4.2 [Differential Pivot Attachment](4_final_steps.md#42-differential-pivot-attachment)
   - 4.3 [Front Wheels](4_final_steps.md#43-front-wheels)
   - 4.4 [Rear Wheels](4_final_steps.md#44-rear-wheels)

Further information on wiring and the inner components of the rover can be found in the electrical guides.

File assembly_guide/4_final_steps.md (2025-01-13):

# Mechanical Assembly Guide

## 4 Final Steps



#### Assembly Steps

- 4.1 [Rocker Bogie Insertion](#41-rocker-bogie-insertion)
- 4.2 [Differential Pivot Attachment](#42-differential-pivot-attachment)
- 4.3 [Front Wheels](#43-front-wheels)
- 4.4 [Rear Wheels](#44-rear-wheels)
- [Required Parts (Final Steps)](#required-parts-final-steps)

### 4.1 Rocker Bogie Insertion

#### Required Parts

| Amount | Part | Part Number | Link |
| :----: | --- | --- | --- |
| 1 | [Main Body](1_main_body.md) | | |
| 2 | [Rocker Bogie (L/R)](3_rocker_bogie.md) | | |
| 2 (1)  | 1506 Series 32mm ID Spacer (36mm OD, **6mm Length**) - 2 Pack | 1506-0032-0006 | https://www.gobilda.com/1506-series-32mm-id-spacer-36mm-od-6mm-length-2-pack/ |
| 2 (1)  | goTUBE Endcap (14mm Bore, 36mm OD, 4mm Thick) - 4 Pack | 1519-0014-0400 | https://www.gobilda.com/gotube-endcap-14mm-bore-36mm-od-4mm-thick-4-pack/ |
| 8 | `M4 x 10mm` Button Head Screw | | |
| 8 | `M4 x 0.1mm` Washer | | |

#### Assembly Info

Insert the _Rocker Bogie_ into the _Main Body_, slide another spacer ring onto the end of the _goRAIL_ and screw the _goTUBE Endcap_ onto it using four 10mm button head screws.

> ⚠️ Use washers between screw heads and plastic parts!

#### 4.1.1 Insert Left Rocker Bogie

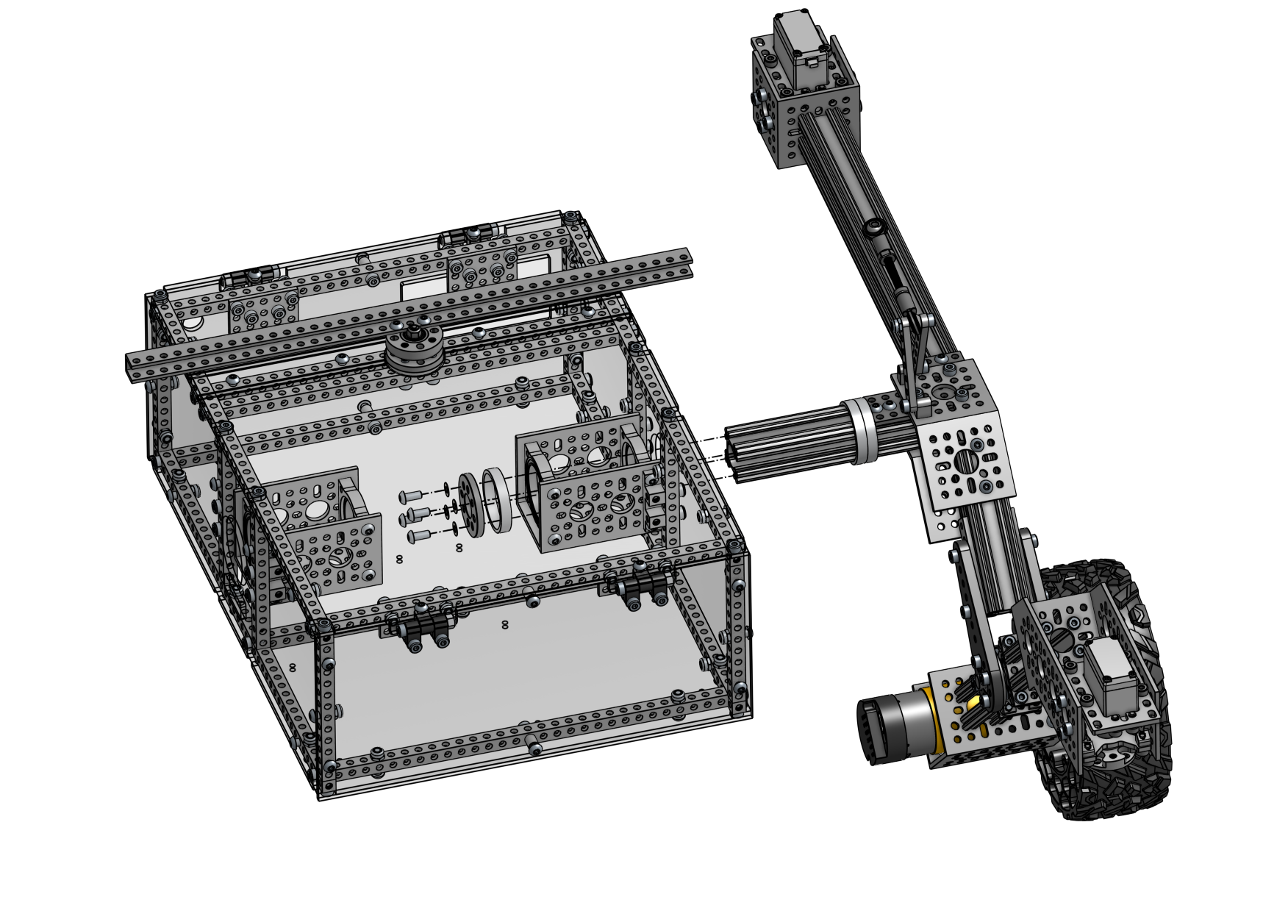
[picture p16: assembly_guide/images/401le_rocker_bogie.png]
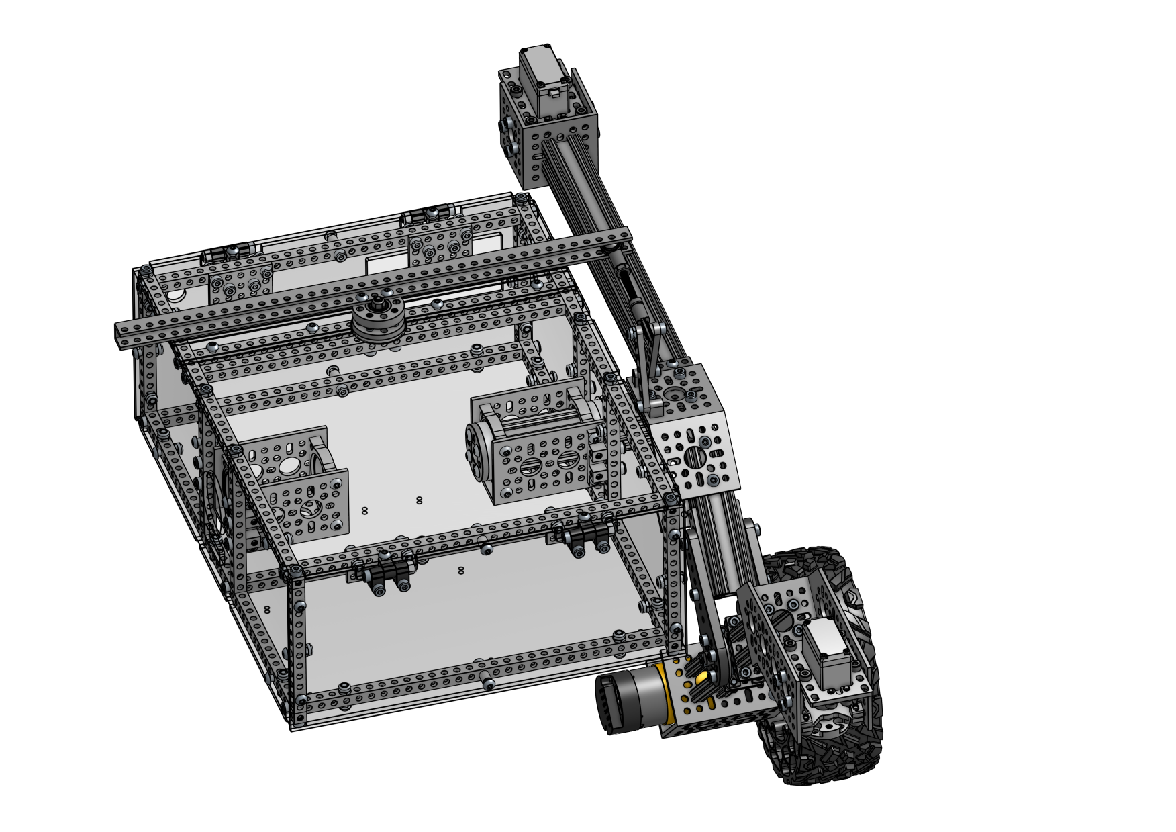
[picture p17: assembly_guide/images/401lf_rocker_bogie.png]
 

#### 4.1.2 Insert Right Rocker Bogie

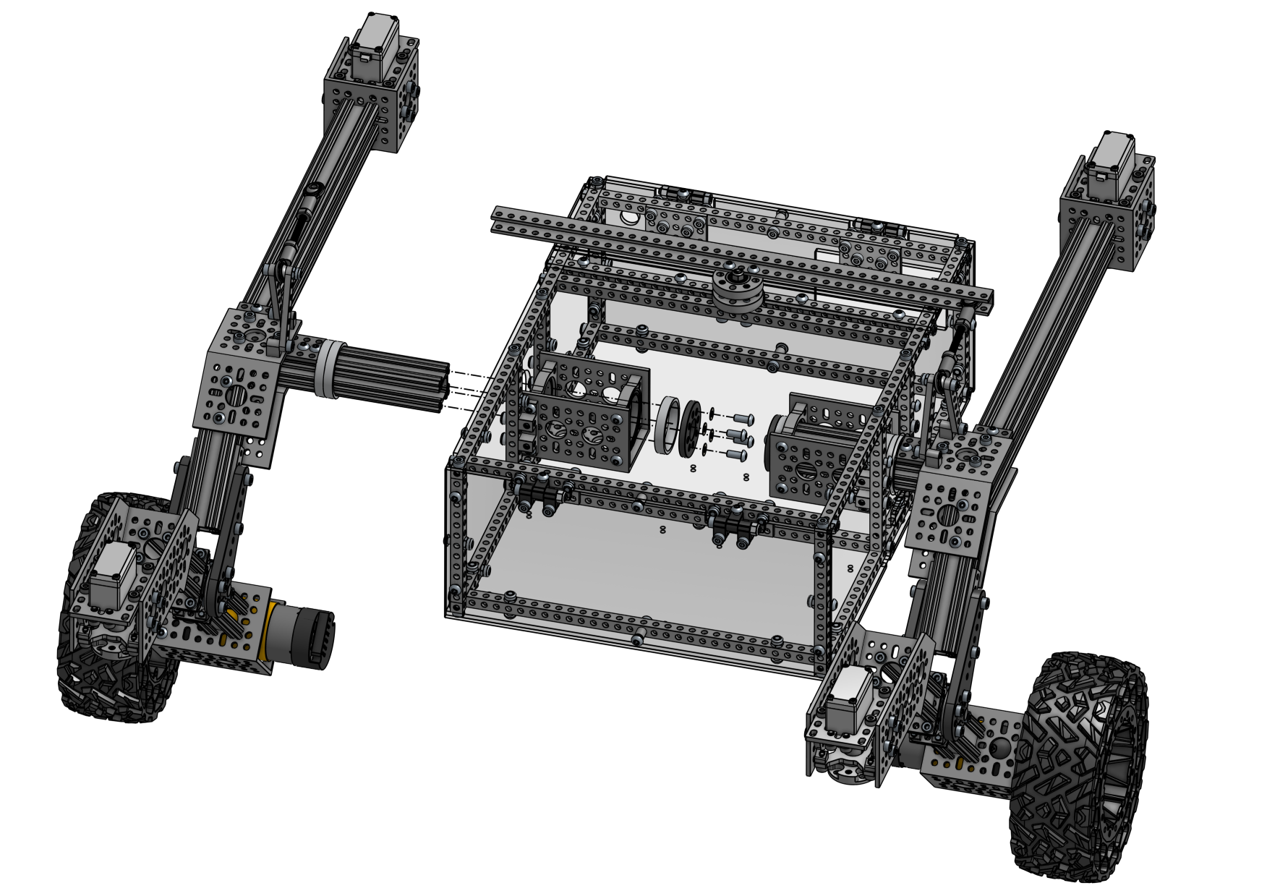
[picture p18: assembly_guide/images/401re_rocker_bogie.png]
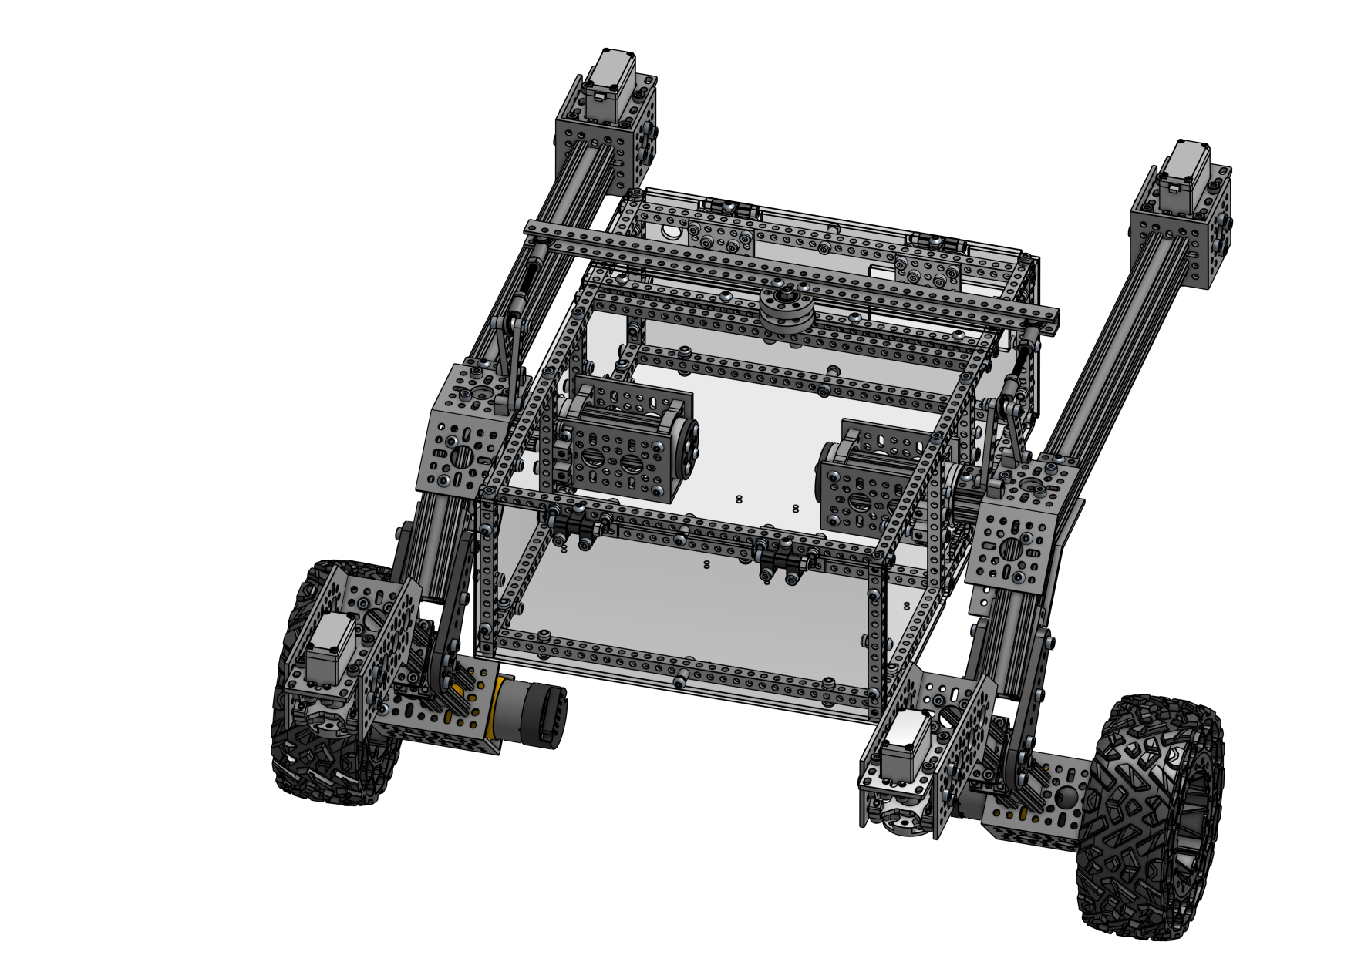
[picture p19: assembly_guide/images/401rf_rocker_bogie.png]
 

### 4.2 Differential Pivot Attachment

#### Required Parts

| Amount | Part | Part Number | Link |
| :----: | --- | --- | ---- |
| 2 | `M4 x 20mm` Socket Head Screw | | |
| 2 | `M4` Nylock Nut | | |

#### Assembly Info

Insert the loose _Steel Ball Bearings_ of the _Rocker Bogies_ into the _U-Channel_ on top of the _Main Body_. Secure them in hole `2` (counting from each end) with a 20mm socket head screw and Nylock nut.

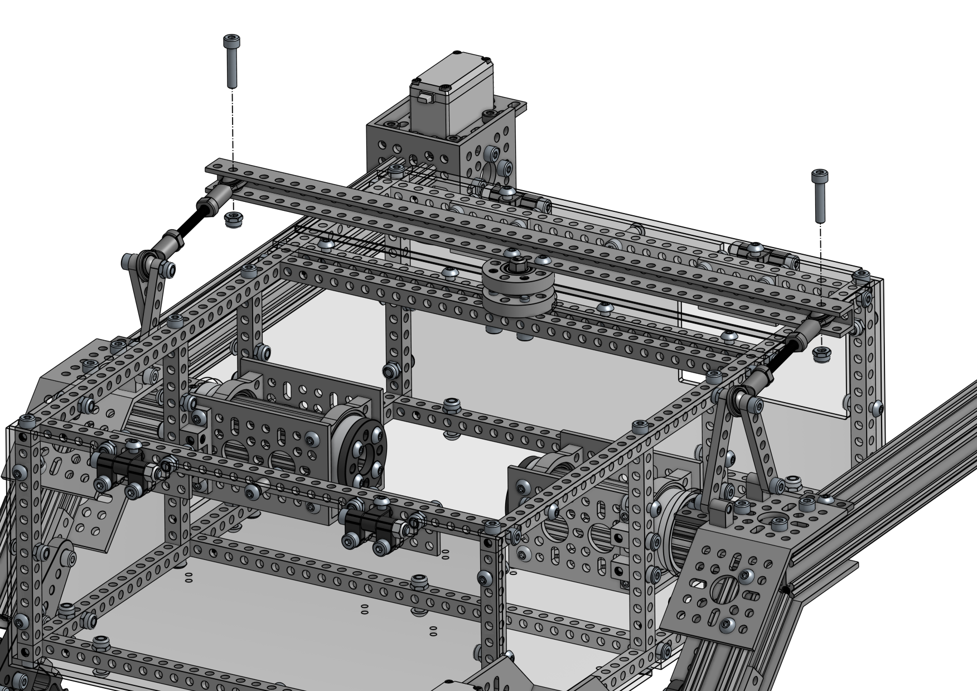
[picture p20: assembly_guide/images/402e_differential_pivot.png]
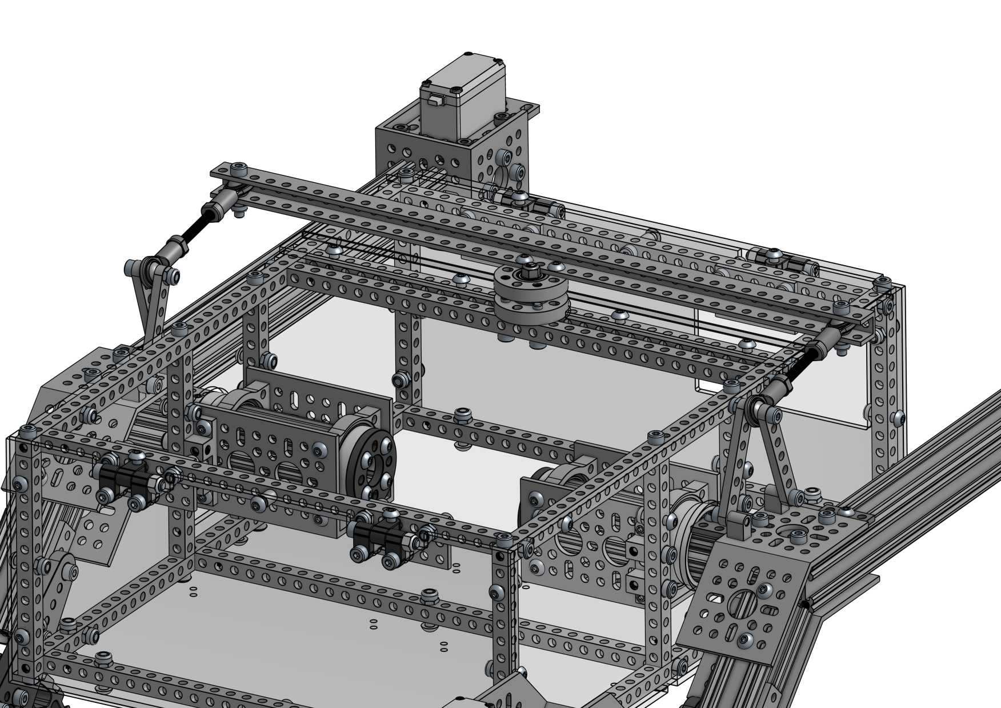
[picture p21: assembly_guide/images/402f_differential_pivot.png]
 

### 4.3 Front Wheels

#### Required Parts

| Amount | Part | Part Number | Link |
| :----: | --- | --- | ---- |
| 2 | [Corner Wheel (L/R)](2_wheels.md#21-corner-wheels-2l2r) | | |
| 8 | `M4 x 8mm` Socket Head Screw | | |

#### Assembly Info

> ⚠️ **Center the servos before installing the wheels!**  
> Upload the provided [servo_centering.ino](../arduino_servo_centering/arduino_servo_centering.ino) sketch to an Arduino compatible device.
> Connect the red wire (VCC) of the servo to the 5V pin on the Arduino.
> Connect the black wire (GND) of the servo to one of the GND pins on the Arduino.
> Connect the white wire (signal) of the servo to pin 9 on the Arduino.

Once the servo is centered, one of the non-threaded holes of the servo shaft should point _exactly_ to the front of the rover. If necessary, remove the servo shaft and reinstall it in the correct orientation. Attach the _Corner Wheels_ to the servo shafts using four 12mm socket head screws.

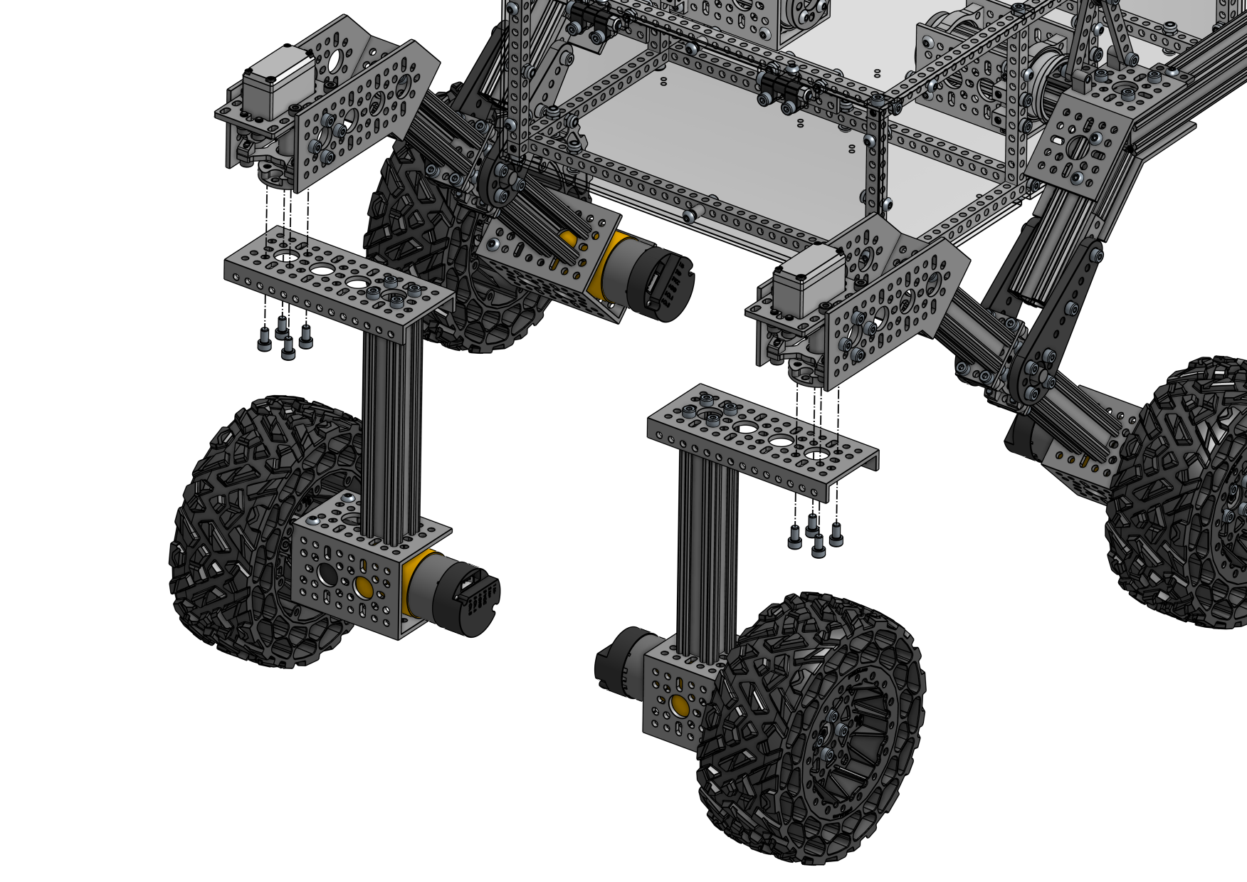
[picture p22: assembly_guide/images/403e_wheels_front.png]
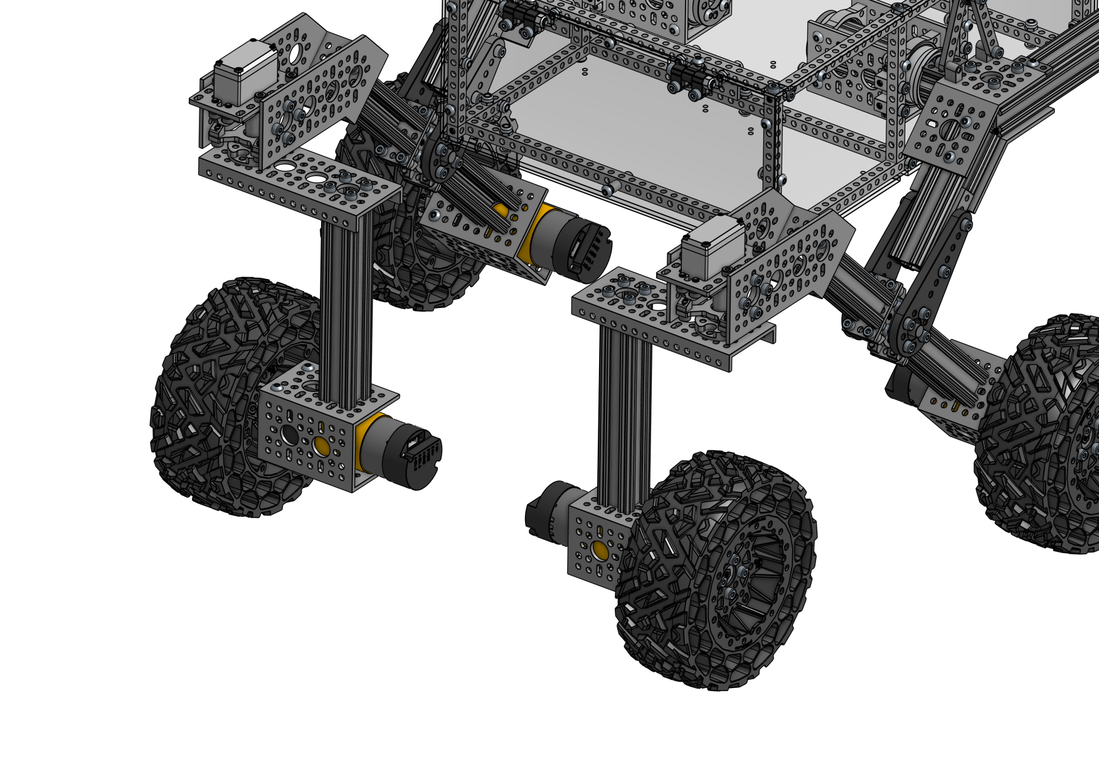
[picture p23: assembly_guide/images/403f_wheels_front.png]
 

### 4.4 Rear Wheels

#### Required Parts

| Amount | Part | Part Number | Link |
| :----: | --- | --- | ---- |
| 2 | [Corner Wheel (L/R)](2_wheels.md#21-corner-wheels-2l2r) | | |
| 8 | `M4 x 8mm` Socket Head Screw | | |

#### Assembly Info

> ⚠️ **Center the servos before installing the wheels!**  
> Upload the provided [servo_centering.ino](../arduino_servo_centering/arduino_servo_centering.ino) sketch to an Arduino compatible device.
> Connect the red wire (VCC) of the servo to the 5V pin on the Arduino.
> Connect the black wire (GND) of the servo to one of the GND pins on the Arduino.
> Connect the white wire (signal) of the servo to pin 9 on the Arduino.

Once the servo is centered, one of the non-threaded holes of the servo shaft should point _exactly_ to the back of the rover. If necessary, remove the servo shaft and reinstall it in the correct orientation. Attach the _Corner Wheels_ to the servo shafts using four 12mm socket head screws.

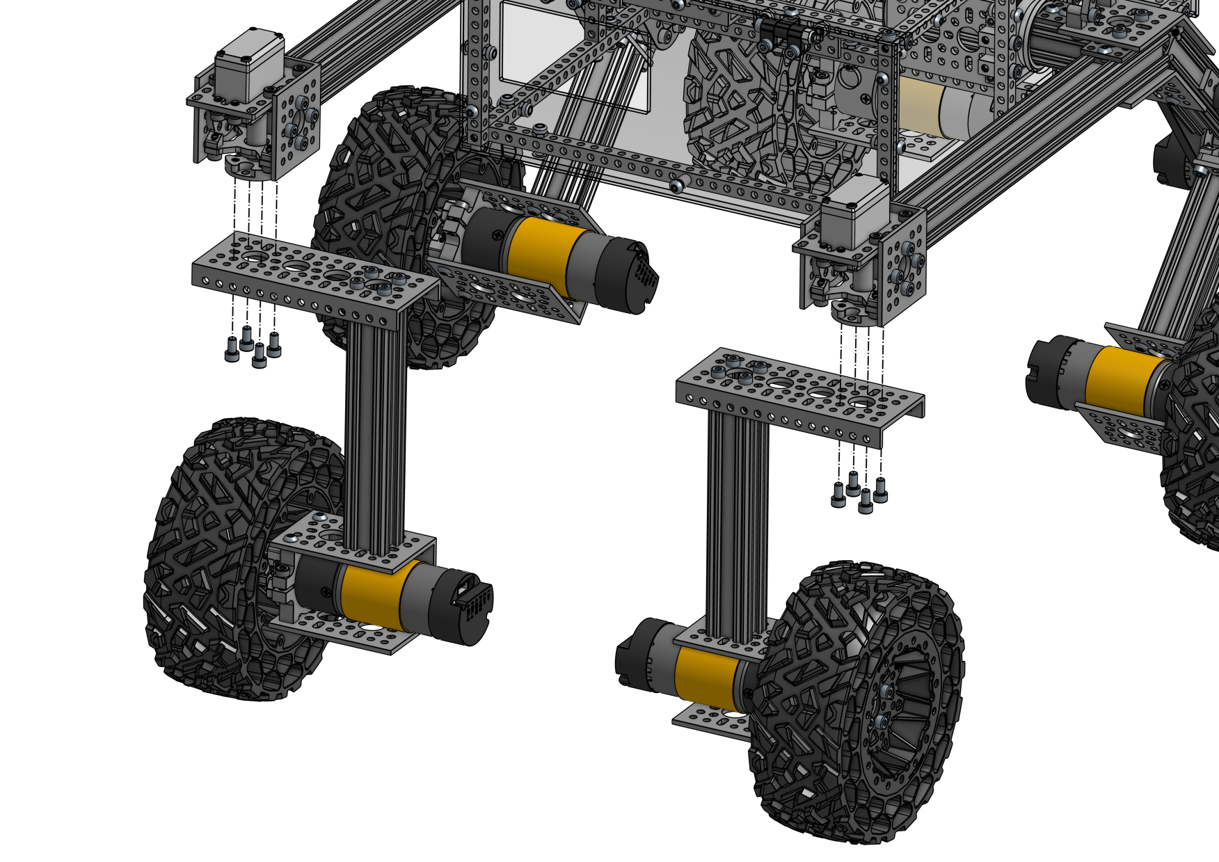
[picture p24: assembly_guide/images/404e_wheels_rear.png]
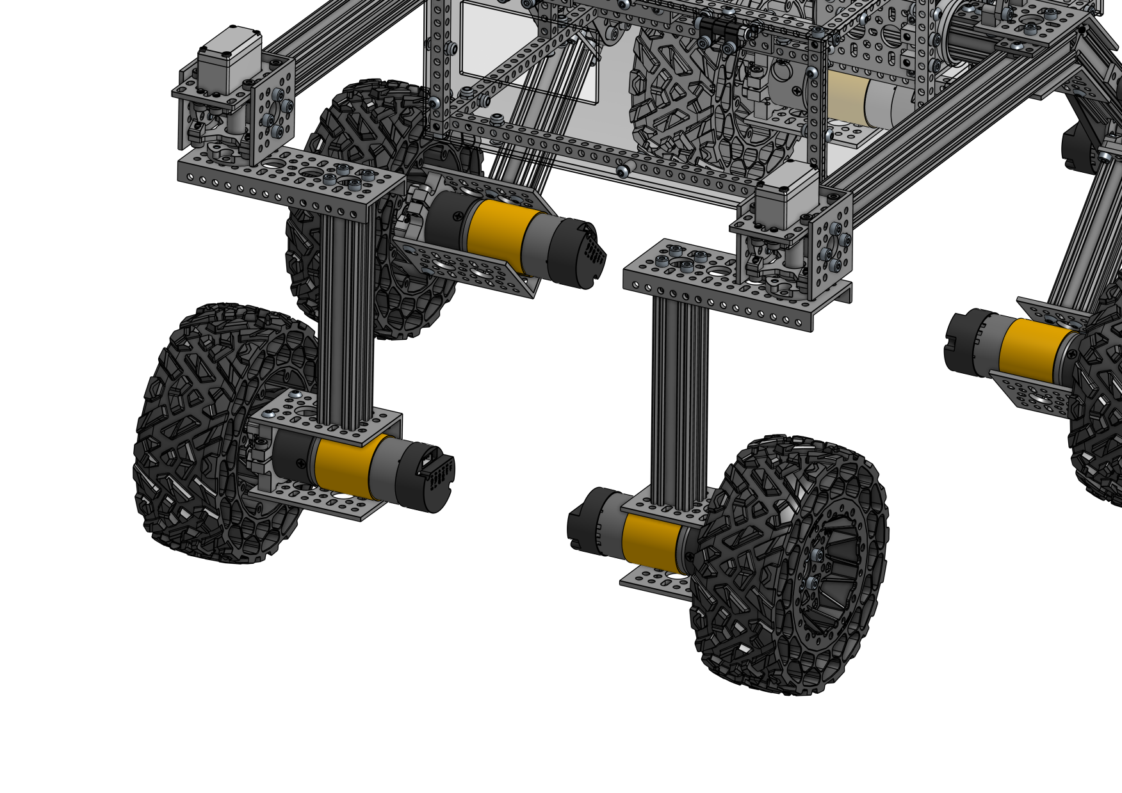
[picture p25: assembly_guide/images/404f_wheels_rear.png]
 

### Next Steps

> 🎉 Congratulations on building your own little mars rover!

- [x] [1 Main Body](1_main_body.md)
- [x] [2 Wheels](2_wheels.md)
- [x] [3 Rocker Bogie](3_rocker_bogie.md)
- [x] 4 Final Steps

Continue with the electrical guides to bring your rover to life!

### Required Parts (Final Steps)

This is a summary of all parts required in this chapter.

| Amount | Part | Part Number | Link |
| :----: | --- | --- | --- |
| 2 (1)  | 1506 Series 32mm ID Spacer (36mm OD, **6mm Length**) - 2 Pack | 1506-0032-0006 | https://www.gobilda.com/1506-series-32mm-id-spacer-36mm-od-6mm-length-2-pack/ |
| 2 (1)  | goTUBE Endcap (14mm Bore, 36mm OD, 4mm Thick) - 4 Pack | 1519-0014-0400 | https://www.gobilda.com/gotube-endcap-14mm-bore-36mm-od-4mm-thick-4-pack/ |
| 8 | `M4 x 10mm` Button Head Screw | | |
| 16 | `M4 x 8mm` Socket Head Screw | | |
| 2 | `M4 x 20mm` Socket Head Screw | | |
| 2 | `M4` Nylock Nut | | |
| 8 | `M4 x 0.1mm` Washer | | |

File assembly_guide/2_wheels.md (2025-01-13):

# Mechanical Assembly Guide

## 2 Wheels



#### Assembly Steps

- 2.1 [Corner Wheels (2L/2R)](#21-corner-wheels-2l2r)
- 2.2 [Middle Wheels (L/R)](#22-middle-wheels-lr)
- [Required Parts (Wheels)](#required-parts-wheels)

### 2.1 Corner Wheels (2L/2R)

#### Required Parts

| Amount | Part | Part Number | Link |
| :----: | --- | --- | --- |
| 4 | Wasteland Wheel (**144mm Diameter**, **52mm Width**) | 3616-0014-0144 | https://www.gobilda.com/wasteland-wheel-144mm-diameter-52mm-width/ |
| 4 | 5203 Series Yellow Jacket Planetary Gear Motor (26.9:1 Ratio, **24mm Length** **8mm REX™** Shaft, **223 RPM**, 3.3 - 5V Encoder) | 5203-2402-0027 | https://www.gobilda.com/5203-series-yellow-jacket-planetary-gear-motor-26-9-1-ratio-24mm-length-8mm-rex-shaft-223-rpm-3-3-5v-encoder/ |
| 4 | 1310 Series Hyper Hub (**8mm REX™** Bore) | 1310-0016-4008 | https://www.gobilda.com/1310-series-hyper-hub-8mm-rex-bore/ |
| 4 | 1401 Series 2-Side, 2-Post Clamping Mount (**43mm Width**, **36mm Bore**) | 1401-0043-0036 | https://www.gobilda.com/1401-series-2-side-2-post-clamping-mount-43mm-width-36mm-bore/ |
| 4 | 1120 Series U-Channel (**2 Hole**, 72mm Length) | 1120-0002-0072 | https://www.gobilda.com/1120-series-u-channel-2-hole-72mm-length/ |
| 4 | 1121 Series Low-Side U-Channel (**4 Hole**, 120mm Length) | 1121-0004-0120 | https://www.gobilda.com/1121-series-low-side-u-channel-4-hole-120mm-length/ |
| 4 | 1109 Series goRAIL (**144mm Length**) | 1109-0024-0144 | https://www.gobilda.com/1109-series-gorail-144mm-length/ |
| 16 | `M4 x 6mm` Button Head Screw | |
| 16 | `M4 x 10mm` Button Head Screw | | |
| 32 | `M4 x 12mm` Socket Head Screw | | |

#### Assembly Info

Screw the _144mm goRAIL_ to the _U-Channel_ first using 10mm button head screws. Install the _Clamping Mount_ with 6mm button head screws and the _Low-Side U-Channel_ with the 12mm socket head screws.

> ⚠️ Remember to feed the required cables through the _goRAIL_ before installing the motor.

Insert the motor into the _Clamping Mount_ so that the dark gray part of the motor lines up with the edge of the _U-Channel_. The _Hyper Hub_ should be flush with the end of the motor shaft Install the wheel using 12mm socket head screws. The deeper side of the wheel should face the _Hyper Hub_ and hide the whole front of the motor.

#### 2.1.1 Left Corner Wheel (2x)

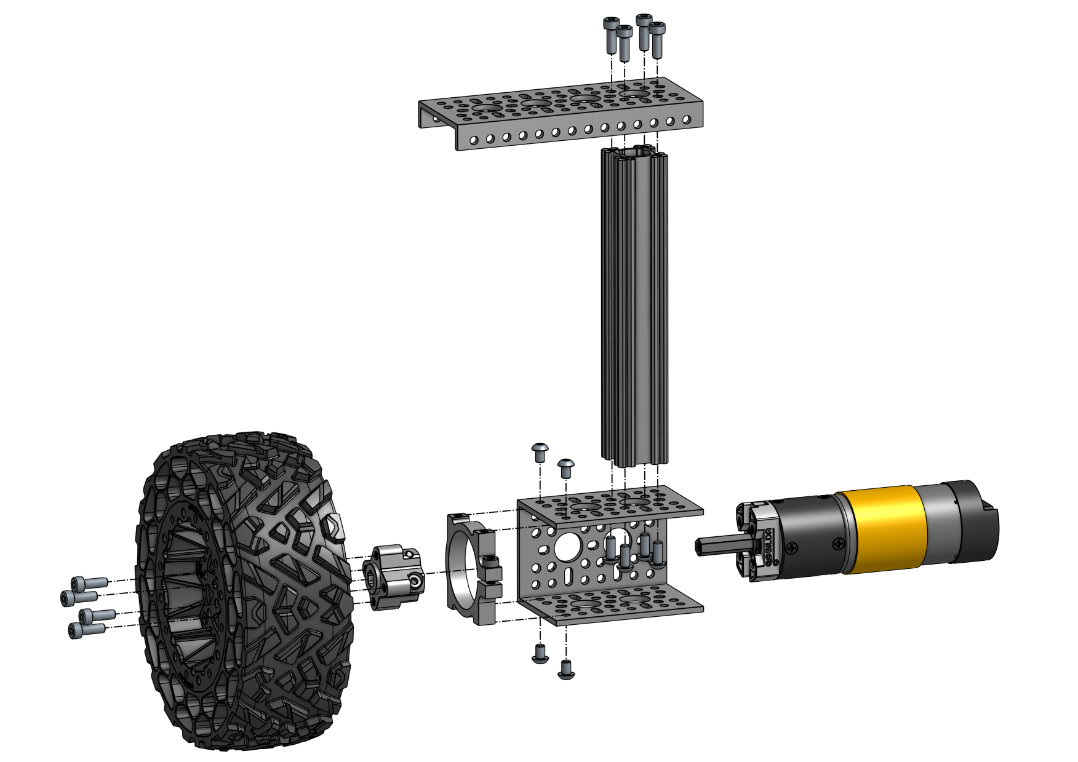
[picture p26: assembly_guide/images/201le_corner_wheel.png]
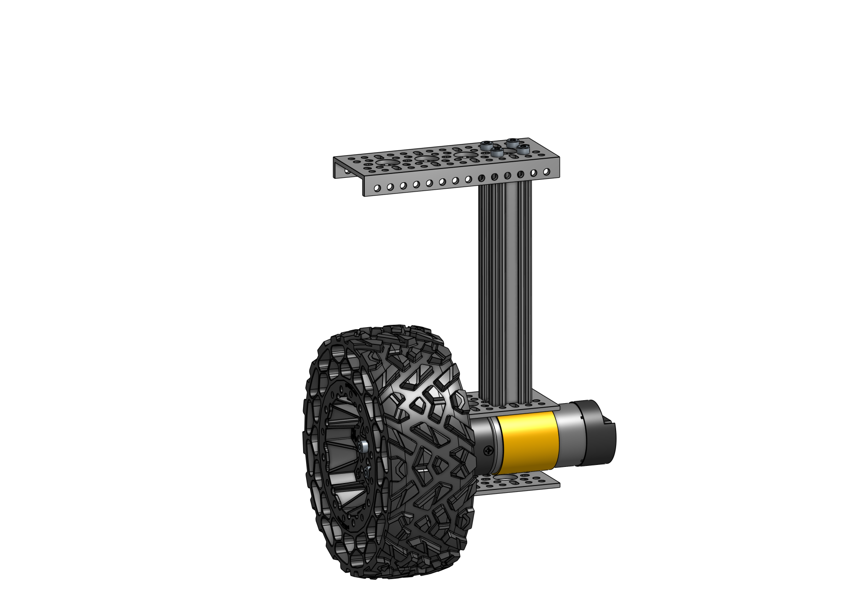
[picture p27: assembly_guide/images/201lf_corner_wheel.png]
 

#### 2.1.2 Right Corner Wheel (2x)

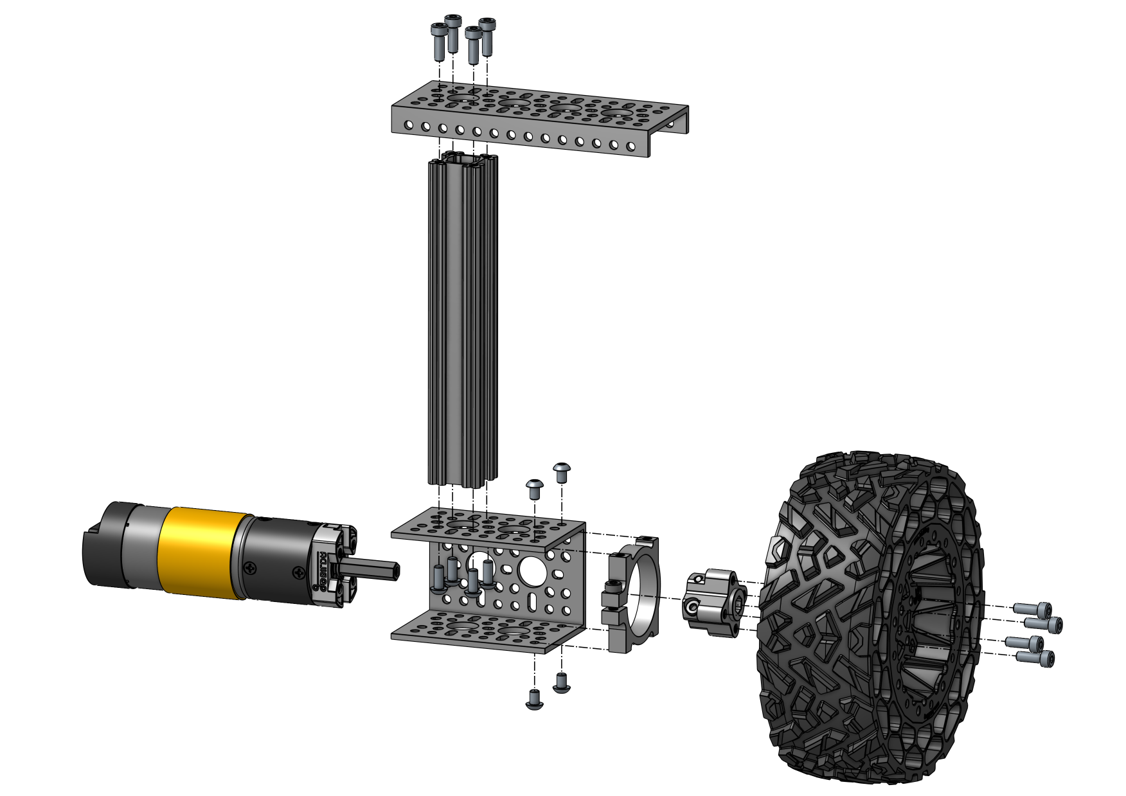
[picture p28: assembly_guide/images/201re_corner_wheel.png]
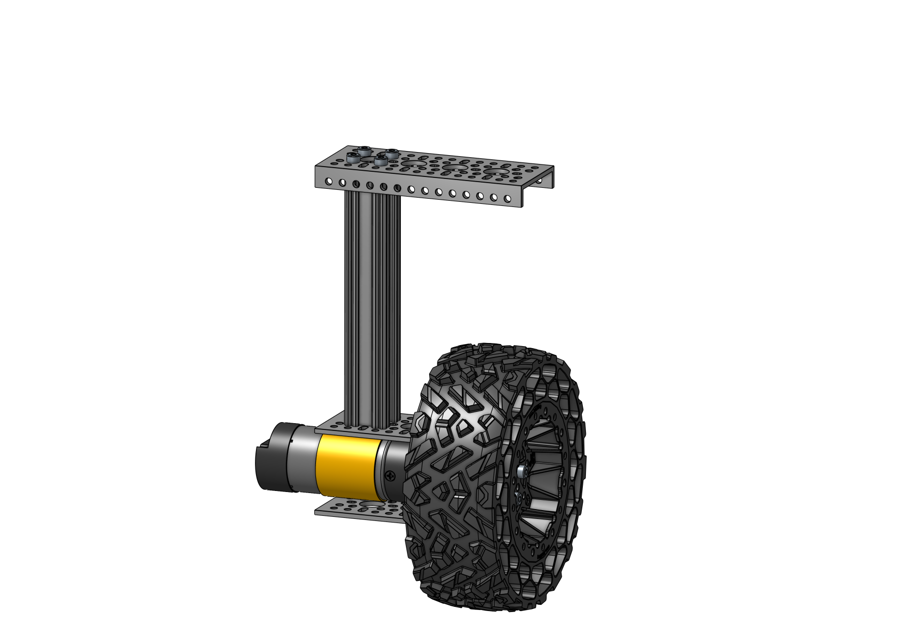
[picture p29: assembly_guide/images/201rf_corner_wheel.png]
 

### 2.2 Middle Wheels (L/R)

#### Required Parts

| Amount | Part | Part Number | Link |
| :----: | --- | --- | --- |
| 2 | Wasteland Wheel (**144mm Diameter**, **52mm Width**) | 3616-0014-0144 | https://www.gobilda.com/wasteland-wheel-144mm-diameter-52mm-width/ |
| 2 | 5203 Series Yellow Jacket Planetary Gear Motor (26.9:1 Ratio, **24mm Length** **8mm REX™** Shaft, **223 RPM**, 3.3 - 5V Encoder) | 5203-2402-0027 | https://www.gobilda.com/5203-series-yellow-jacket-planetary-gear-motor-26-9-1-ratio-24mm-length-8mm-rex-shaft-223-rpm-3-3-5v-encoder/ |
| 2 | 1310 Series Hyper Hub (**8mm REX™** Bore) | 1310-0016-4008 | https://www.gobilda.com/1310-series-hyper-hub-8mm-rex-bore/ |
| 2 | 1401 Series 2-Side, 2-Post Clamping Mount (**43mm Width**, **36mm Bore**) | 1401-0043-0036 | https://www.gobilda.com/1401-series-2-side-2-post-clamping-mount-43mm-width-36mm-bore/ |
| 2 | 1120 Series U-Channel (**2 Hole**, 72mm Length) | 1120-0002-0072 | https://www.gobilda.com/1120-series-u-channel-2-hole-72mm-length/ |
| 2 | 1118 Series Open goRAIL (**96mm Length**) | 1118-0024-0096 | https://www.gobilda.com/1118-series-open-gorail-96mm-length/ |
| 2 | 1116 Series Grid Plate (**3 x 5 Hole**, 24 x 40mm) | 1116-0024-0040 | https://www.gobilda.com/1116-series-grid-plate-3-x-5-hole-24-x-40mm/ |
| 8 | `M4 x 6mm` Button Head Screw | |
| 8 | `M4 x 10mm` Button Head Screw | | |
| 16 | `M4 x 12mm` Socket Head Screw | | |

#### Assembly Info

Screw the _96mm goRAIL_ to the _U-Channel_ first using 10mm button head screws.

> ⚠️ Make sure the open side of the _goRAIL_ points towards the back of the motor away from the wheel!

Install the _Clamping Mount_ with 6mm button head screws and the _Grid Plate_ with the 12mm socket head screws.

> ⚠️ Make sure to install the _3 x 5 Grid Plate_ in the correct orientation. It should be perpendicular to the motor.

Remember to feed the required cables through the _goRAIL_ before installing the motor. Insert the motor into the _Clamping Mount_ so that the dark gray part of the motor lines up with the edge of the _U-Channel_. The _Hyper Hub_ should be flush with the end of the motor shaft Install the wheel using 12mm socket head screws. The deeper side of the wheel should face the _Hyper Hub_ and hide the whole front of the motor.

#### 2.2.1 Left Middle Wheel

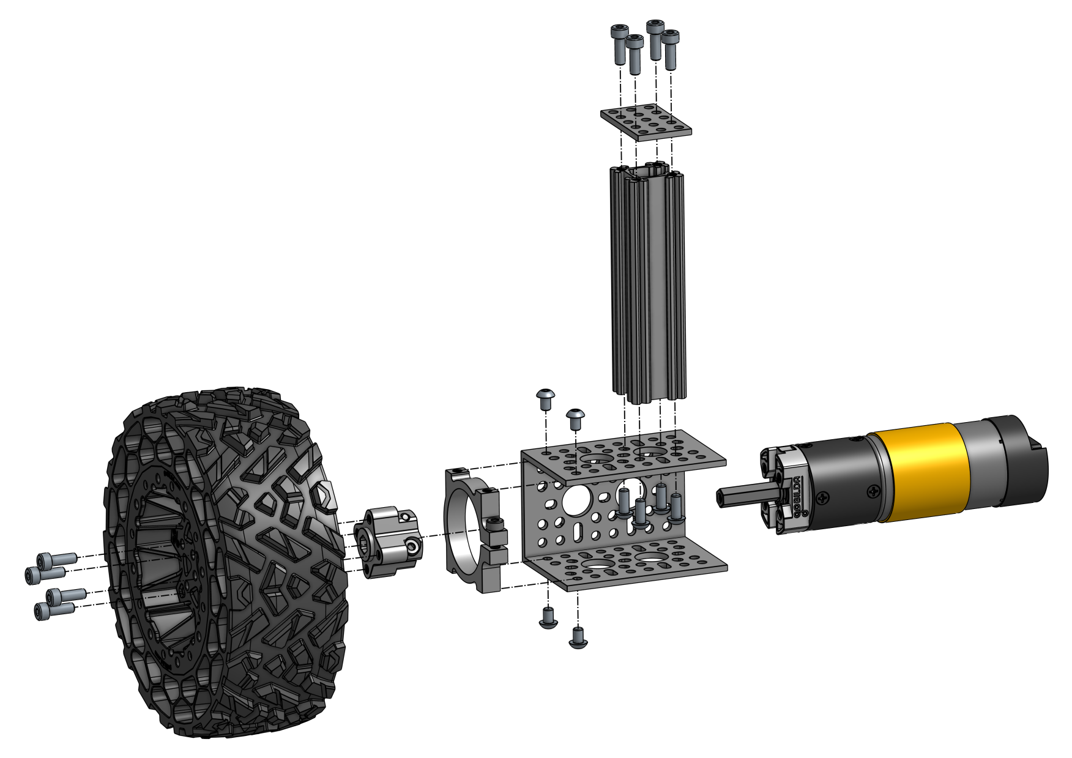
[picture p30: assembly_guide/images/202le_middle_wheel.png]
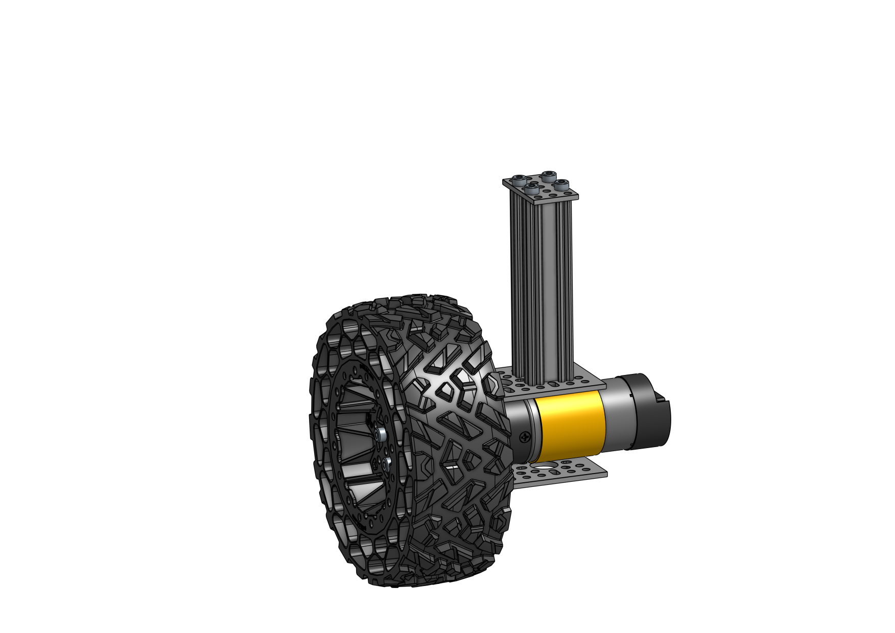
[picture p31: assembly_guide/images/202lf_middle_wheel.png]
 

#### 2.2.2 Right Middle Wheel

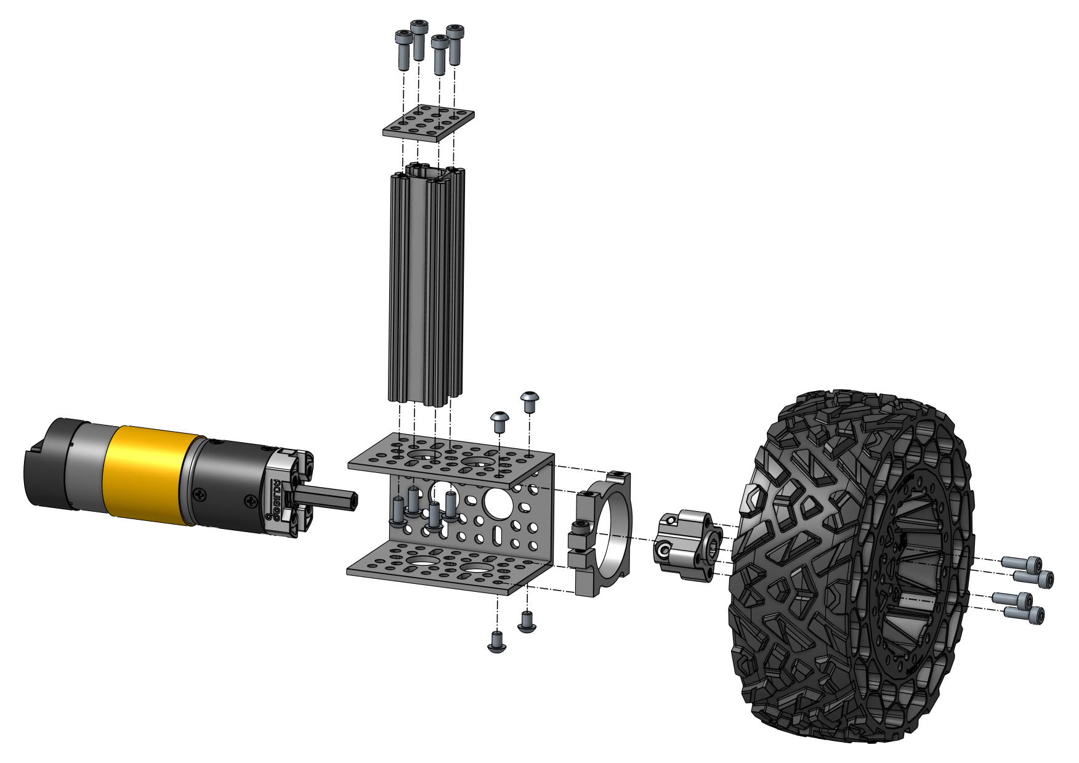
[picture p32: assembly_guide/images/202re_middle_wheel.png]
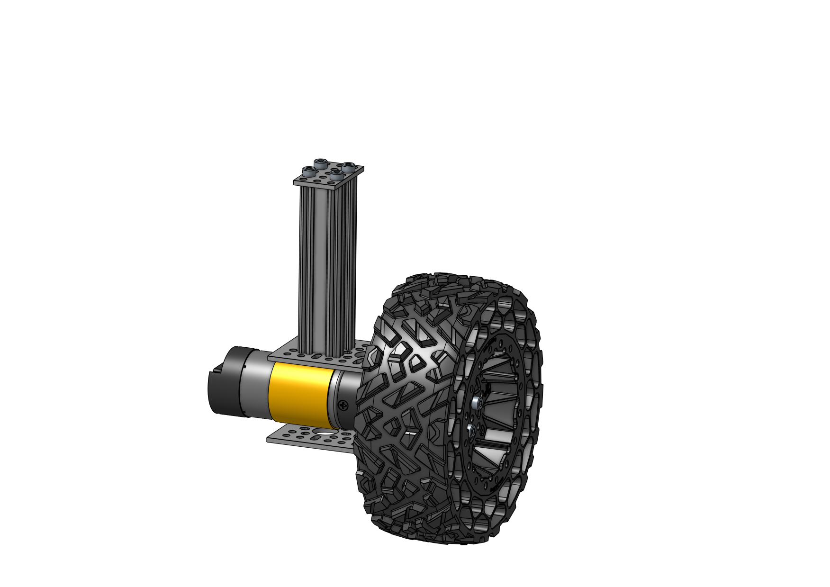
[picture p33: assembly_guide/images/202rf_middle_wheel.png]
 

### Next Steps

> 🎉 Congratulations on completing the wheel assembly!

- [x] [1 Main Body](1_main_body.md)
- [x] 2 Wheels
- [ ] [3 Rocker Bogie](3_rocker_bogie.md)
- [ ] [4 Final Steps](4_final_steps.md)

Continue with building the [Rocker Bogie](3_rocker_bogie.md)!

### Required Parts (Wheels)

This is a summary of all parts required in this chapter.

| Amount | Part | Part Number | Link |
| :----: | --- | --- | --- |
| 4 | 1109 Series goRAIL (**144mm Length**) | 1109-0024-0144 | https://www.gobilda.com/1109-series-gorail-144mm-length/ |
| 2 | 1116 Series Grid Plate (**3 x 5 Hole**, 24 x 40mm) | 1116-0024-0040 | https://www.gobilda.com/1116-series-grid-plate-3-x-5-hole-24-x-40mm/ |
| 2 | 1118 Series Open goRAIL (**96mm Length**) | 1118-0024-0096 | https://www.gobilda.com/1118-series-open-gorail-96mm-length/ |
| 6 | 1120 Series U-Channel (**2 Hole**, 72mm Length) | 1120-0002-0072 | https://www.gobilda.com/1120-series-u-channel-2-hole-72mm-length/ |
| 4 | 1121 Series Low-Side U-Channel (**4 Hole**, 120mm Length) | 1121-0004-0120 | https://www.gobilda.com/1121-series-low-side-u-channel-4-hole-120mm-length/ |
| 6 | 1310 Series Hyper Hub (**8mm REX™** Bore) | 1310-0016-4008 | https://www.gobilda.com/1310-series-hyper-hub-8mm-rex-bore/ |
| 6 | 1401 Series 2-Side, 2-Post Clamping Mount (**43mm Width**, **36mm Bore**) | 1401-0043-0036 | https://www.gobilda.com/1401-series-2-side-2-post-clamping-mount-43mm-width-36mm-bore/ |
| 6 | Wasteland Wheel (**144mm Diameter**, **52mm Width**) | 3616-0014-0144 | https://www.gobilda.com/wasteland-wheel-144mm-diameter-52mm-width/ |
| 6 | 5203 Series Yellow Jacket Planetary Gear Motor (26.9:1 Ratio, **24mm Length** **8mm REX™** Shaft, **223 RPM**, 3.3 - 5V Encoder) | 5203-2402-0027 | https://www.gobilda.com/5203-series-yellow-jacket-planetary-gear-motor-26-9-1-ratio-24mm-length-8mm-rex-shaft-223-rpm-3-3-5v-encoder/ |
| 24 | `M4 x 6mm` Button Head Screw | |
| 24 | `M4 x 10mm` Button Head Screw | | |
| 48 | `M4 x 12mm` Socket Head Screw | | |

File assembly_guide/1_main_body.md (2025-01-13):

# Mechanical Assembly Guide

## 1 Main Body



#### Assembly Steps

- 1.1 [Aluminum Frame](#11-aluminum-frame)
- 1.2 [Wall Standoffs](#12-wall-standoffs)
- 1.3 [Axis Clamps (2x)](#13-axis-clamps-2x)
- 1.4 [Axis Clamp Installation](#14-axis-clamp-installation)
- 1.5 [Top Plate Hinges (4x)](#15-top-plate-hinges-4x)
- 1.6 [Top Plate Hinge Installation](#16-top-plate-hinge-installation)
- 1.7 [Bottom Plate](#17-bottom-plate)
- 1.8 [Side Plates](#18-side-plates)
- 1.9 [Front and Back Plates](#19-front-and-back-plates)
- 1.10 [Top Plates](#110-top-plates)
- 1.11 [Differential Pivot](#111-differential-pivot)
- [Required Parts (Main Body)](#required-parts-main-body)

### 1.1 Aluminum Frame

#### Required Parts

| Amount | Part | Part Number | Link |
| :----: | --- | --- | --- |
| 4 | 1106 Series Square Beam (**41 Hole**, 328mm Length) | 1106-0041-0328 | https://www.gobilda.com/1106-series-square-beam-41-hole-328mm-length/ |
| 7 | 1106 Series Square Beam (**29 Hole**, 232mm Length) | 1106-0029-0232 | https://www.gobilda.com/1106-series-square-beam-29-hole-232mm-length/ |
| 8 | 1106 Series Square Beam (**12 Hole**, 96mm Length)  | 1106-0012-0096 | https://www.gobilda.com/1106-series-square-beam-12-hole-96mm-length/  |
| 30 | `M4 x 16mm` Socket Head Screw | | |

#### Assembly Info

Top beam mounting positions: `2` `28` `30` `40`  
Bottom beam mounting positions: `2` `18` `40`  
Vertical beam positions: `1` `17` `25` `41`

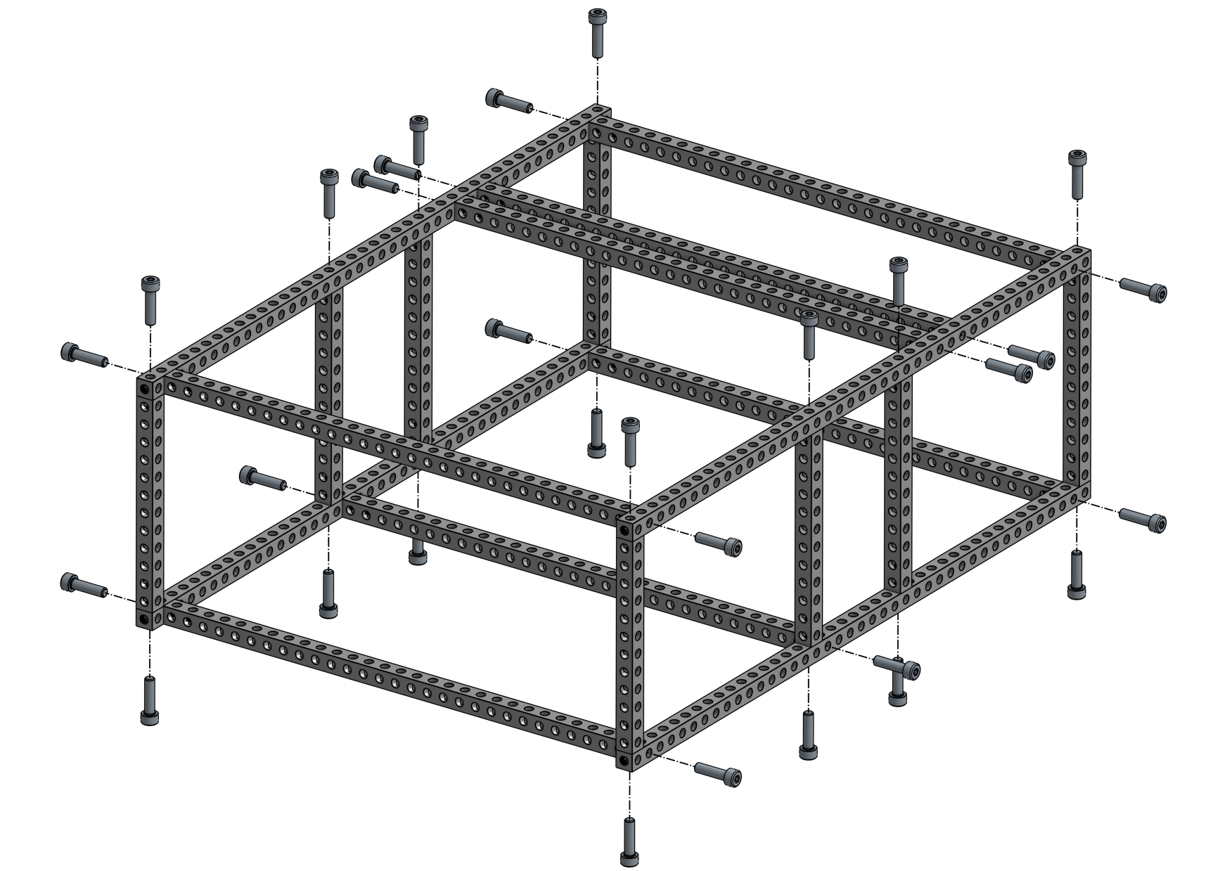
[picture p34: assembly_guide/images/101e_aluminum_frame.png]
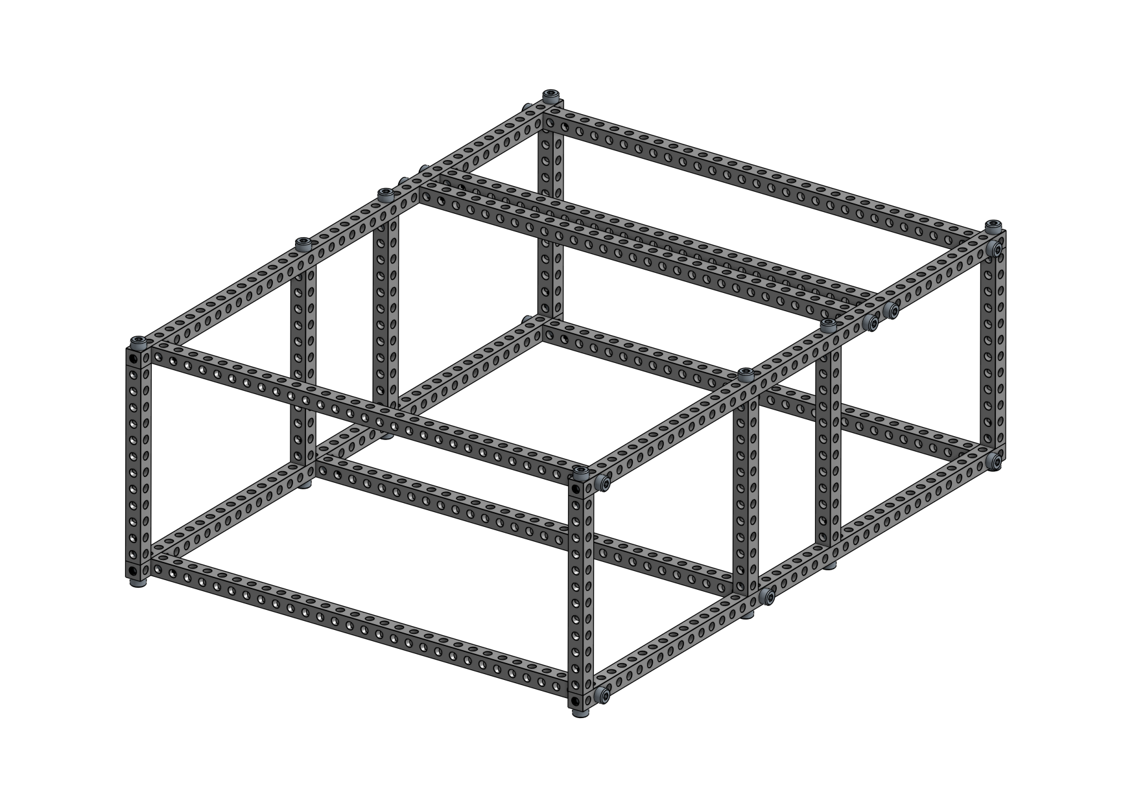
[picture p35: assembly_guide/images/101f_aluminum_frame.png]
 

### 1.2 Wall Standoffs

#### Required Parts

| Amount | Part | Part Number | Link |
| :----: | --- | --- | --- |
| 4 (1)  | 1501 Series M4 x 0.7mm Standoff (**6mm OD**, **8mm Length**) - 4 Pack | 1501-0006-0080 | https://www.gobilda.com/1501-series-m4-x-0-7mm-standoff-6mm-od-8mm-length-4-pack/ |
| 4 | `M4 x 12mm` Socket Head Screw | | |

#### Assembly Info

Standoff mounting position: `15` (center of 29 hole beam)

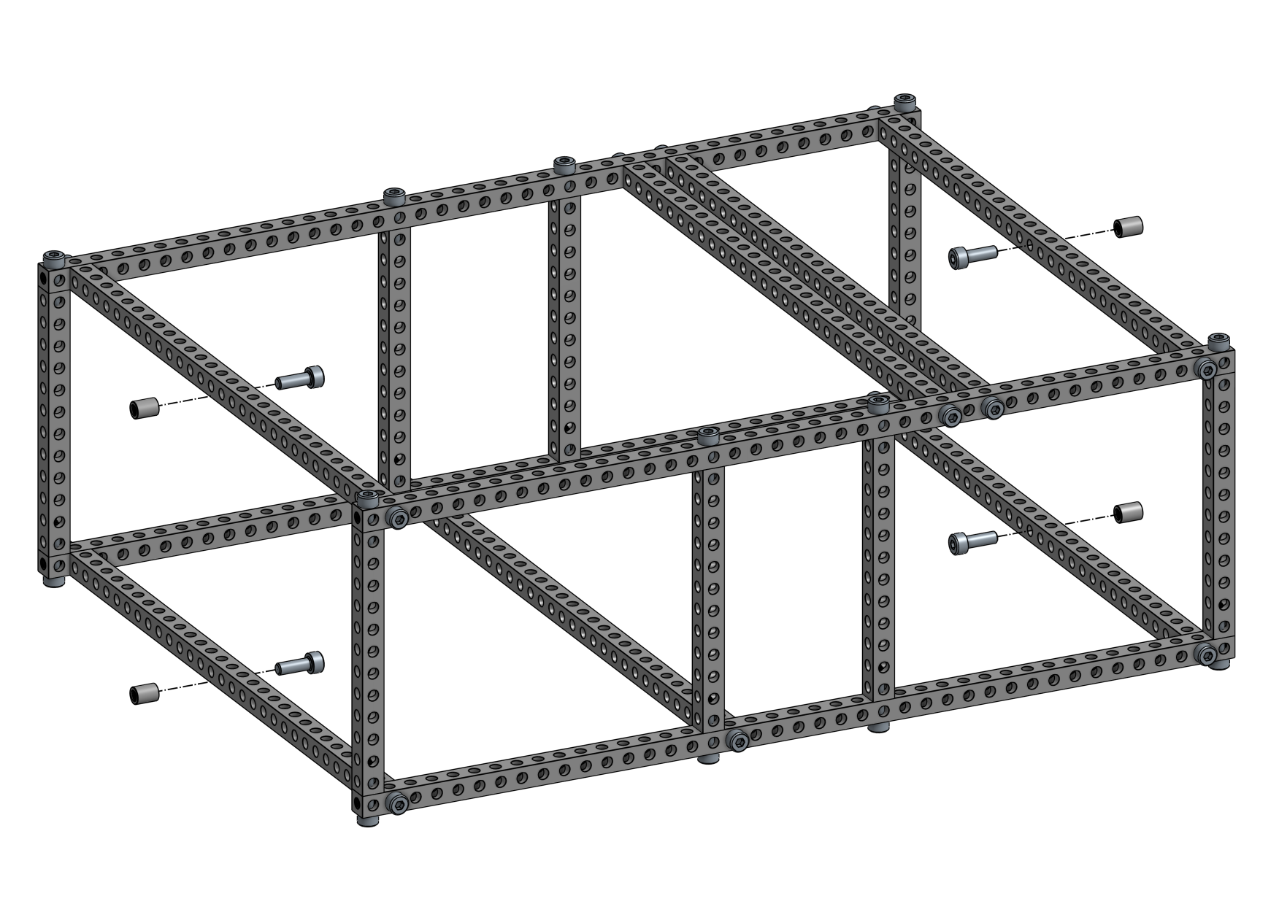
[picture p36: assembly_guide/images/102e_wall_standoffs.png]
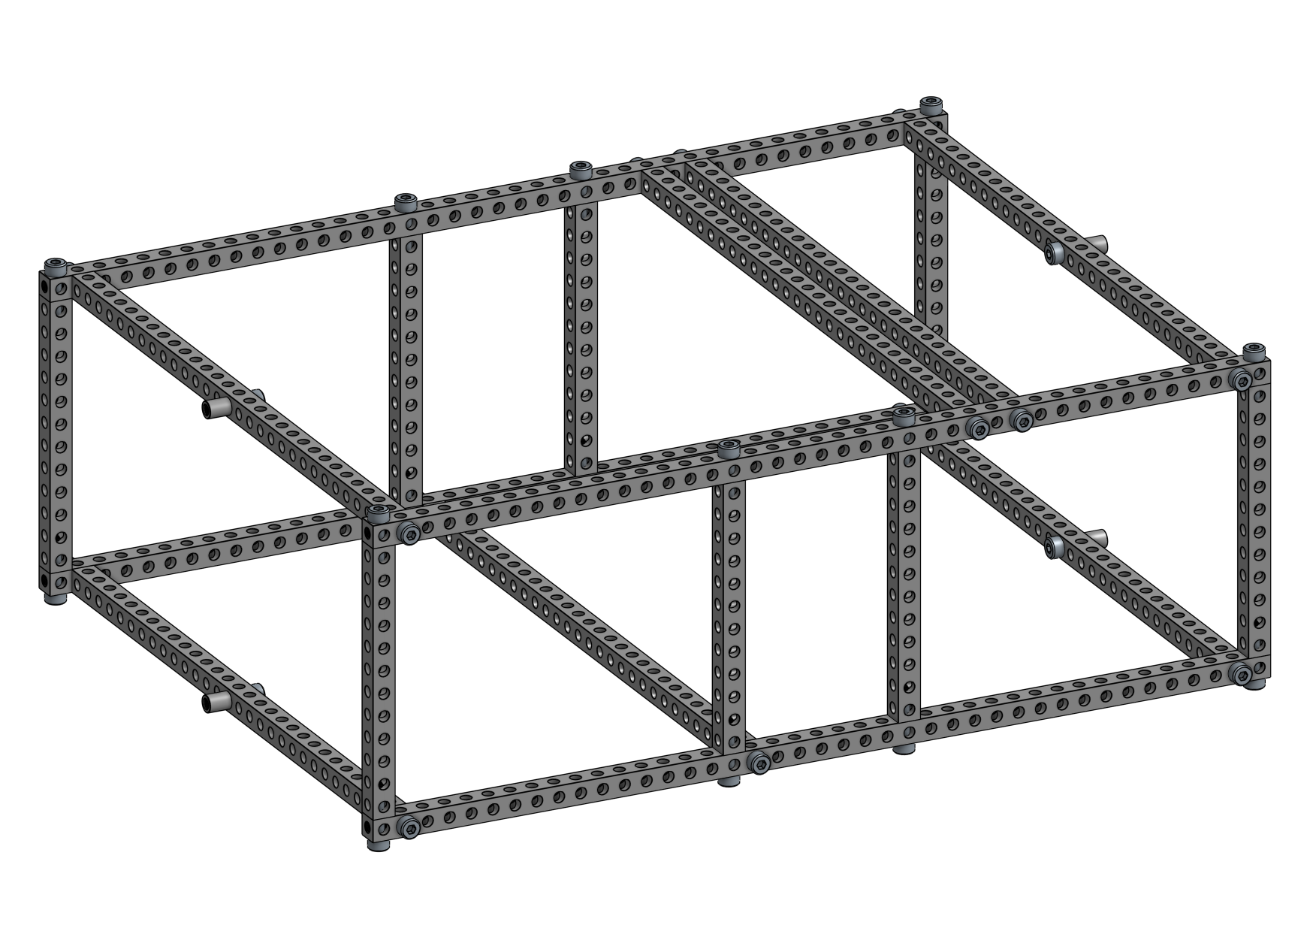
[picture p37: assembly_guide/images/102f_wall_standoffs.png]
 

### 1.3 Axis Clamps (2x)

#### Required Parts

| Amount | Part | Part Number | Link |
| :----: | --- | --- | --- |
| 2 | 1120 Series U-Channel (**2 Hole**, 72mm Length) | 1120-0002-0072 | https://www.gobilda.com/1120-series-u-channel-2-hole-72mm-length/ |
| 4 (2)  | 1205 Series Dual Block Mount (1-4) - 2 Pack | 1205-0001-0004 | https://www.gobilda.com/1205-series-dual-block-mount-1-4-2-pack/ |
| 4 | **32mm** Bore 2-Side, 2-Post Pillow Block (**43mm Width**) | 1604-0043-0032 | https://www.gobilda.com/32mm-bore-2-side-2-post-pillow-block-43mm-width/ |
| 8 | `M4 x 6mm` Button Head Screw | | |
| 8 | `M4 x 10mm` Button Head Screw | | |

#### Assembly Info

> ⚠️ Pay attention to the orientation of the _Pillow Blocks_! The flush sides should face outwards.  
> ⚠️ Pay attention to the orientation of the _Dual Block Mounts_! They should be as near to the edge of the _U-Channel_ as possible.

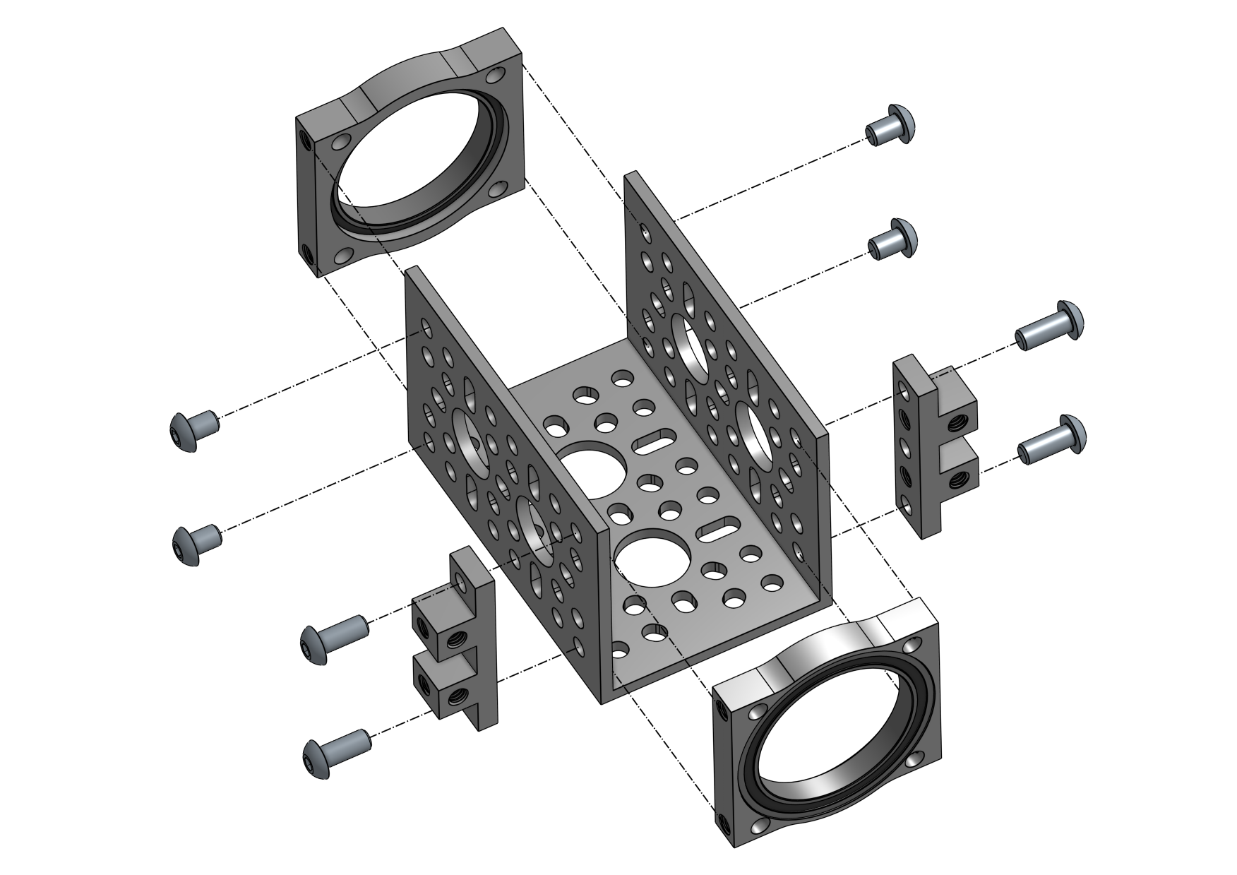
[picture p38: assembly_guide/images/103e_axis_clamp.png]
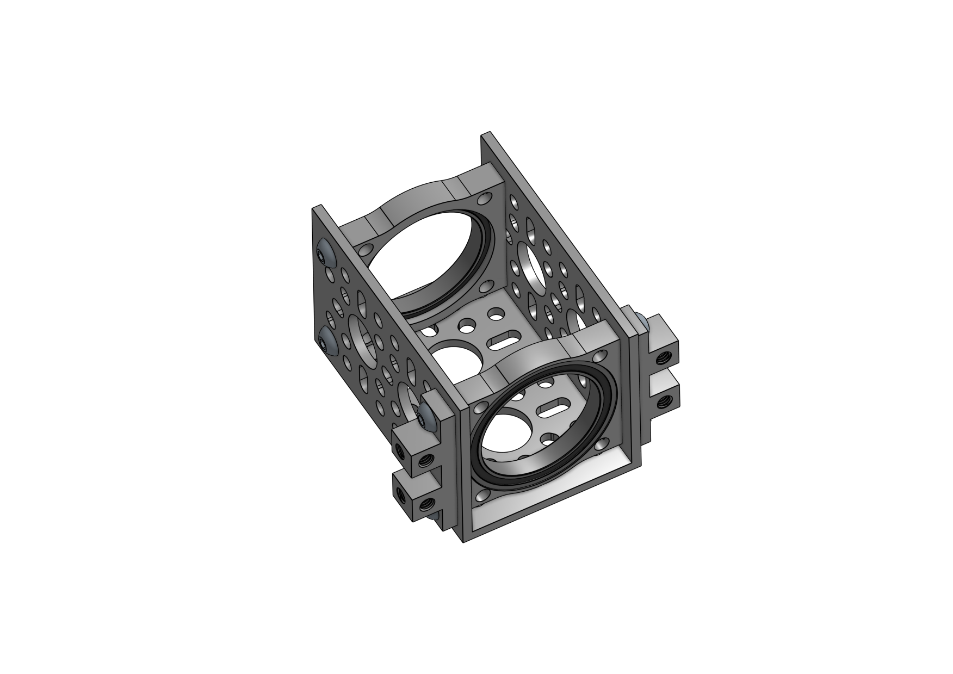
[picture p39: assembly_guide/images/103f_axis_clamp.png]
 

### 1.4 Axis Clamp Installation

| Amount | Part | Part Number | Link |
| :----: | --- | --- | ---- |
| 2 | [Axis Clamp](#13-axis-clamps-2x) | | |
| 8 | `M4 x 16mm` Socket Head Screw | | |

Axis clamp mounting position: `5` `7` (counting from the bottom)

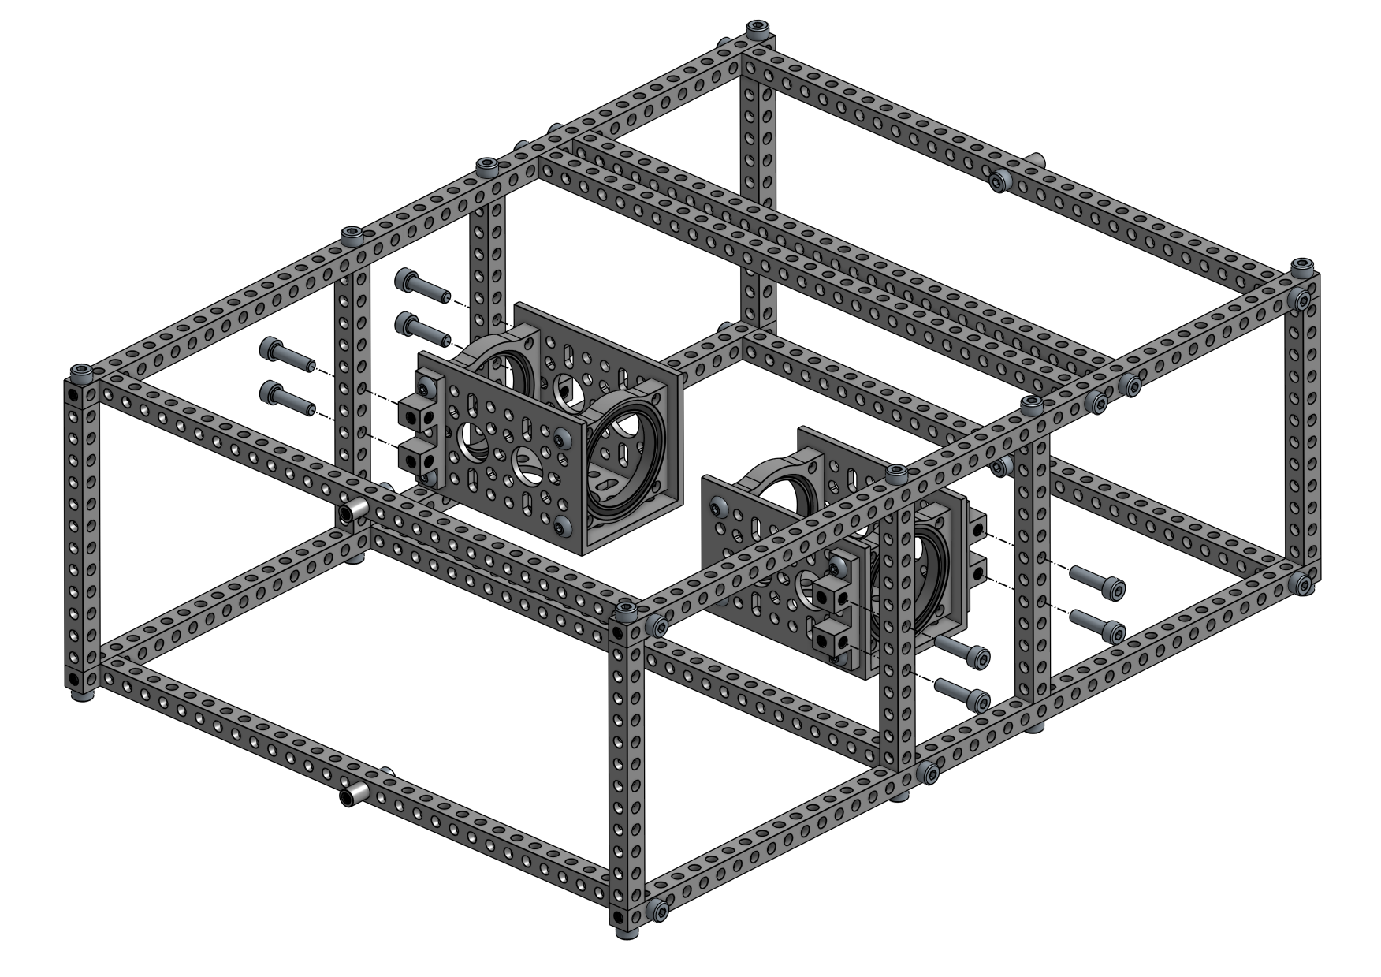
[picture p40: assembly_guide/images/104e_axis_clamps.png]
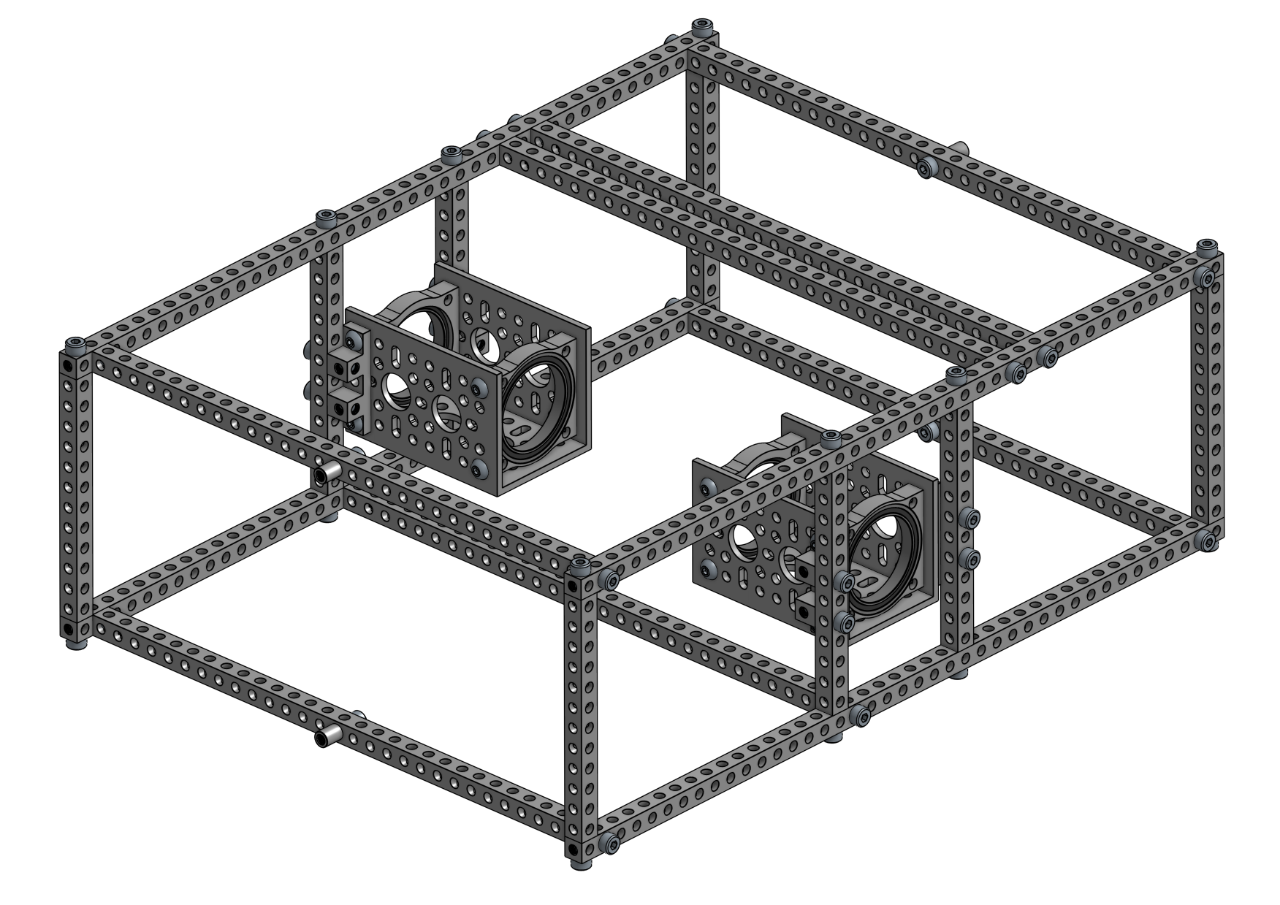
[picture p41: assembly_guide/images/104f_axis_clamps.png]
 

### 1.5 Top Plate Hinges (4x)

#### Required Parts

| Amount | Part | Part Number | Link |
| :----: | --- | --- | --- |
| 4 (2)  | Plastic Hinge - 2 Pack | 2902-0003-0001 | https://www.gobilda.com/plastic-hinge-2-pack/ |
| 8 (2)  | 1501 Series M4 x 0.7mm Standoff (**6mm OD**, **22mm Length**) - 4 Pack | 1501-0006-0220 | https://www.gobilda.com/1501-series-m4-x-0-7mm-standoff-6mm-od-22mm-length-4-pack/ |
| 4 | 1116 Series Grid Plate (**3 x 5 Hole**, 24 x 40mm) | 1116-0024-0040 | https://www.gobilda.com/1116-series-grid-plate-3-x-5-hole-24-x-40mm/ |
| 16 | `M4 x 12mm` Socket Head Screw | | |

#### Assembly Info

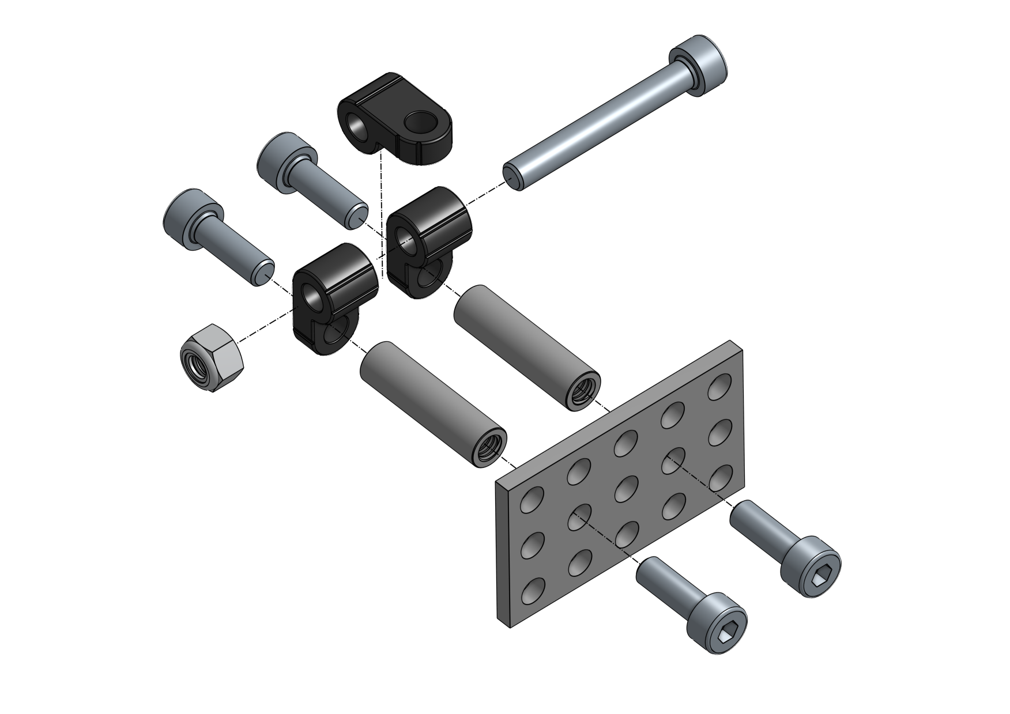
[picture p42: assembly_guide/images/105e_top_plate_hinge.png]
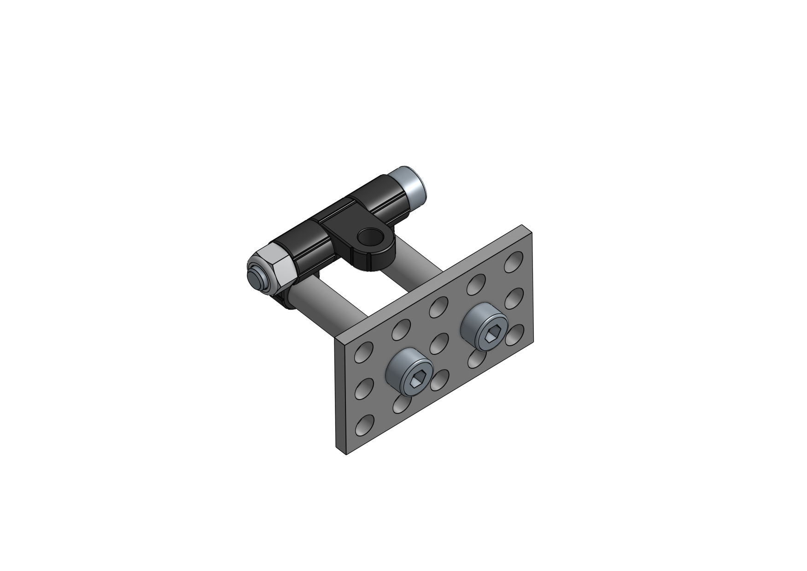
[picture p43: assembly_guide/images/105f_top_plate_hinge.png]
 

### 1.6 Top Plate Hinge Installation

#### Required Parts

| Amount | Part | Part Number | Link |
| :----: | --- | --- | ---- |
| 4 | [Top Plate Hinge](#15-top-plate-hinges-4x) | | |
| 8 | `M4 x 16mm` Socket Head Screw | | |
| 8 | `M4` Nylock Nut | | |

#### Assembly Info

Mounting positions on 29 hole beam: `5` `9` (counting from each edge). The plastic hinge should point up and be flush with the top of the aluminum frame.

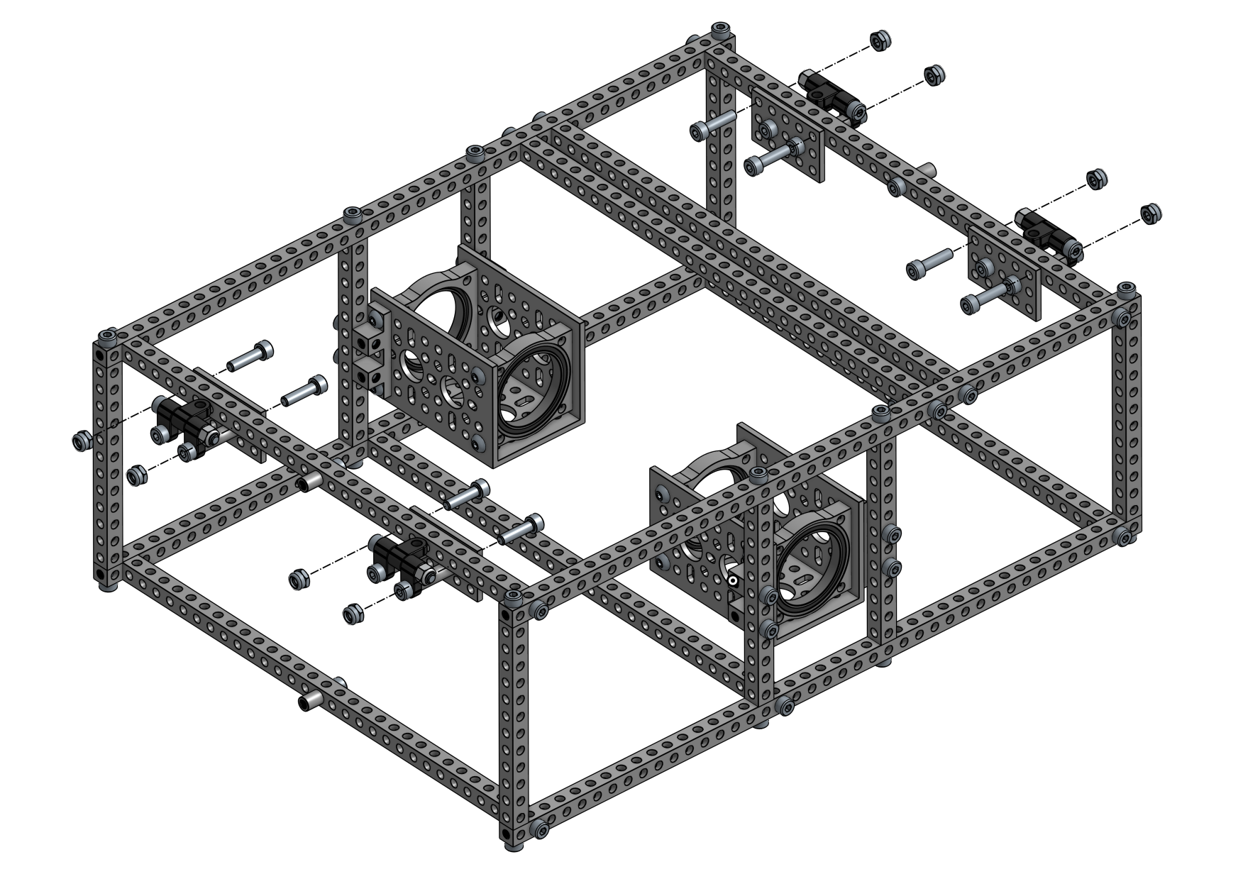
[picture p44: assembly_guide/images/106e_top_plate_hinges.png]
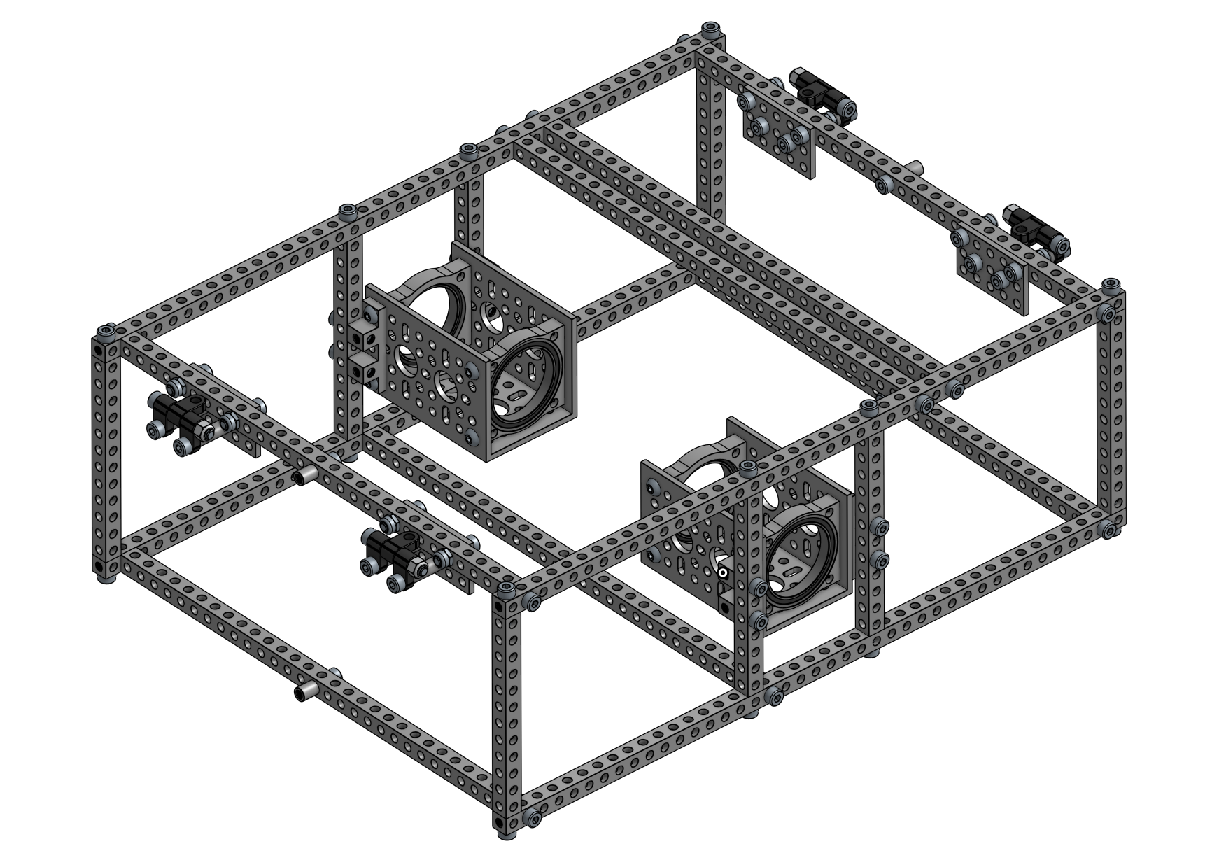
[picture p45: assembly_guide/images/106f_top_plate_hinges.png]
 

### 1.7 Bottom Plate

#### Required Parts

| Amount | Part | Part Number | Link |
| :----: | --- | --- | ---- |
| 1 | Bottom Plate (lasercut) | bottom_plate.dxf | |
| 11 | `M4 x 16mm` Button Head Screw | | |
| 11 | `M4` Nylock Nut | | |

#### Assembly Info

> 🔃 The 3D model is upside down in the following image!

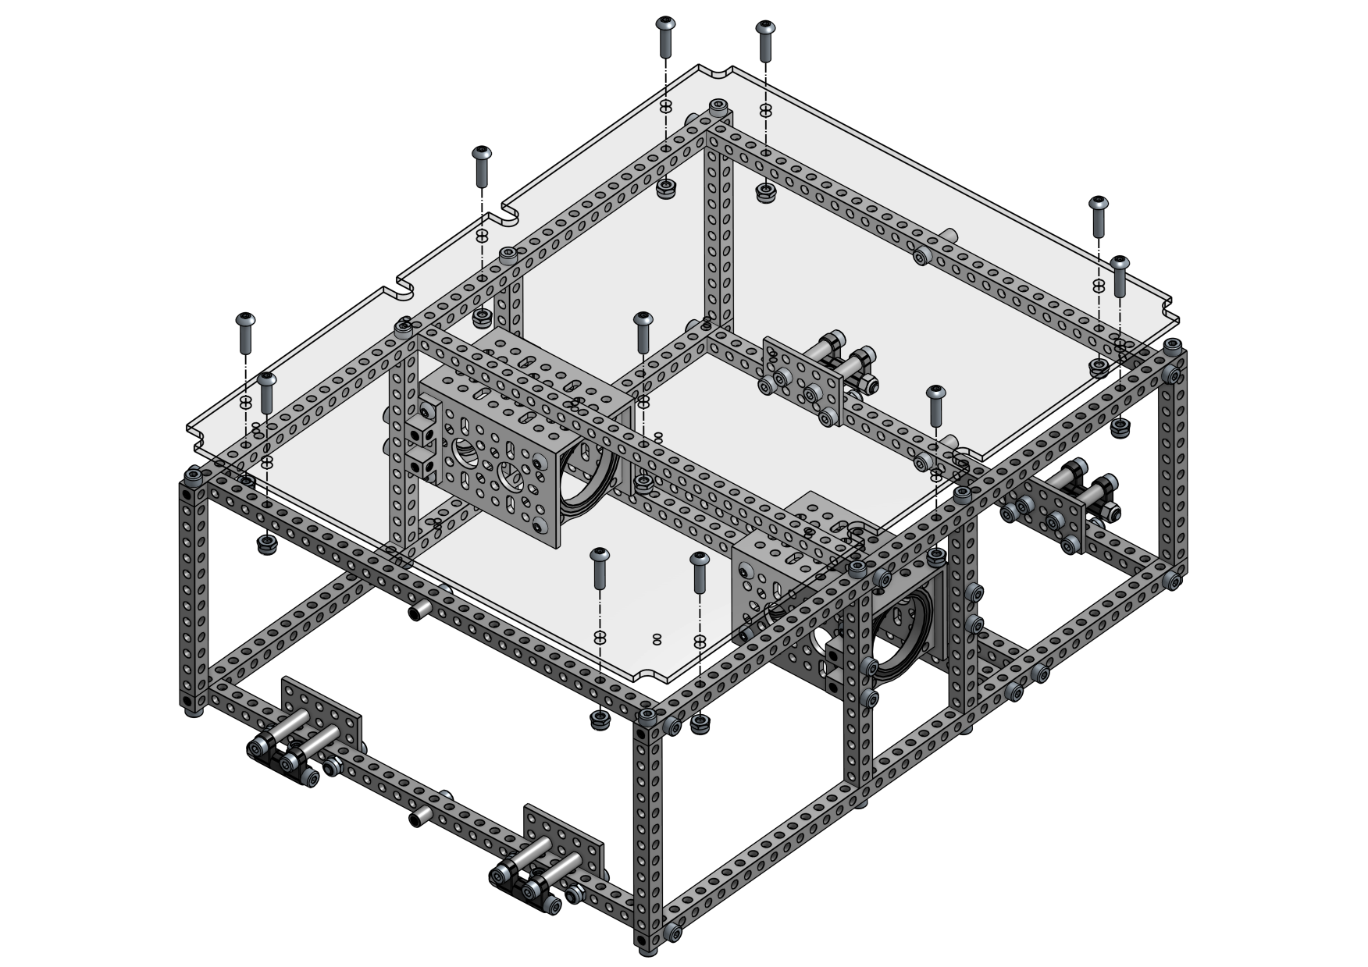
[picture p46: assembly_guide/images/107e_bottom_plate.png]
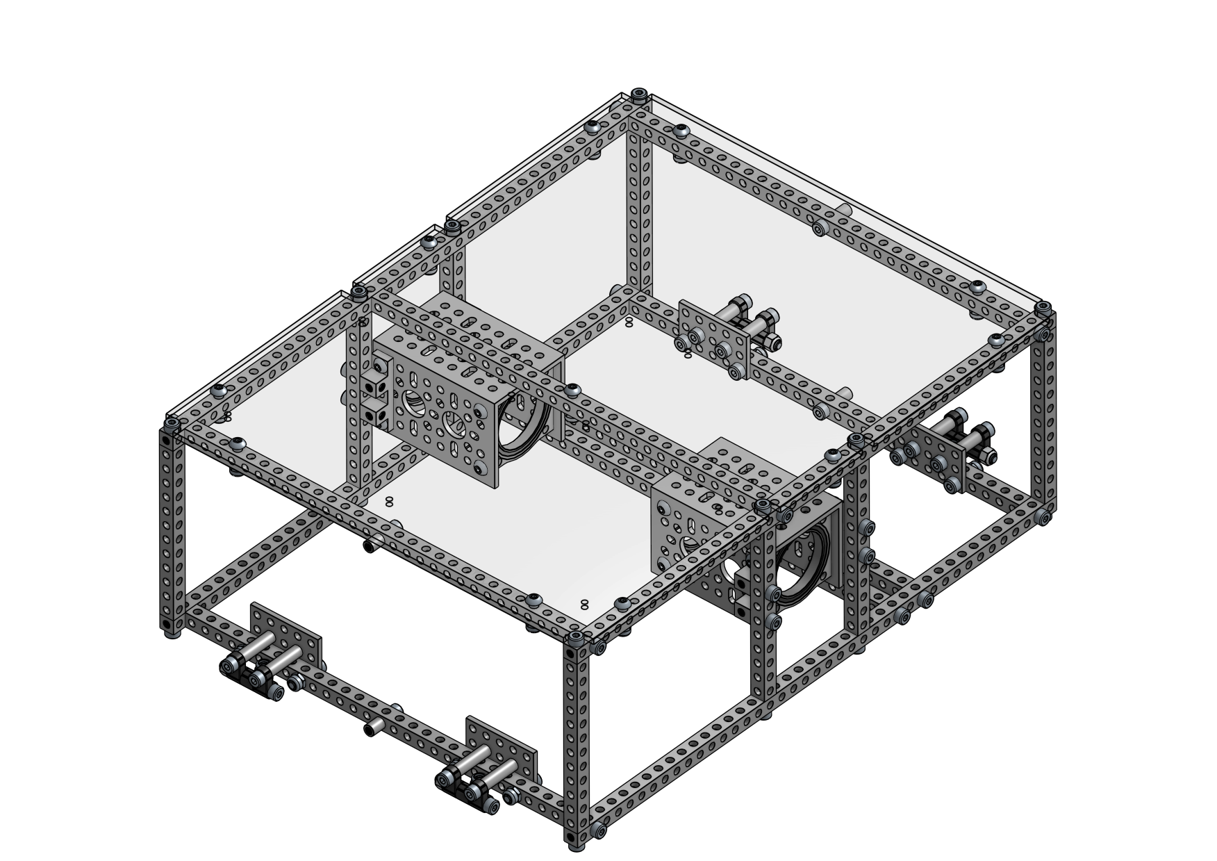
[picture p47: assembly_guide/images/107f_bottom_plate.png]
 

### 1.8 Side Plates

#### Required Parts

| Amount | Part | Part Number | Link |
| :----: | --- | --- | ---- |
| 2 | Side Plate (lasercut) | side_plate.dxf | |
| 16 | `M4 x 16mm` Button Head Screw | | |
| 16 | `M4` Nylock Nut | | |

#### Assembly Info

> 🔃 The 3D model is upside down in the following image!

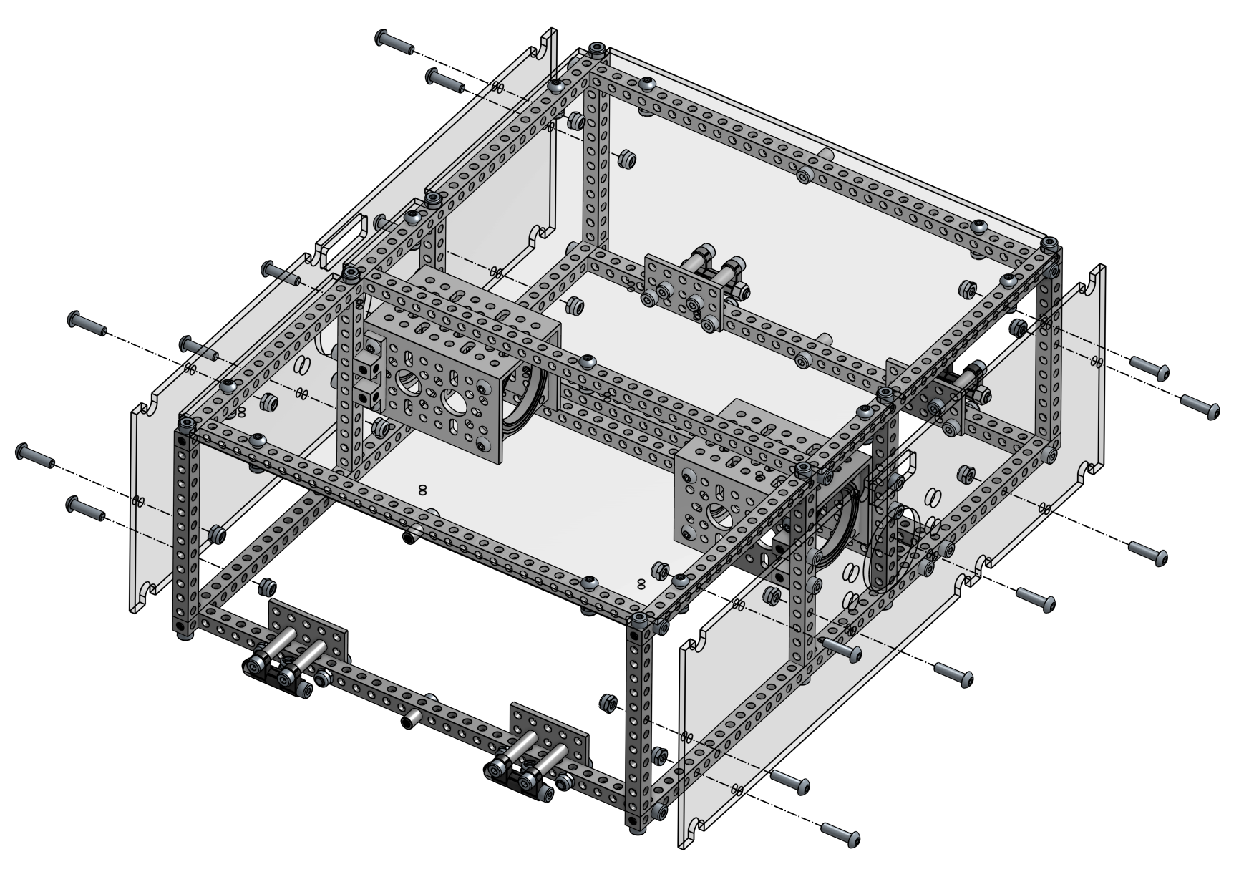
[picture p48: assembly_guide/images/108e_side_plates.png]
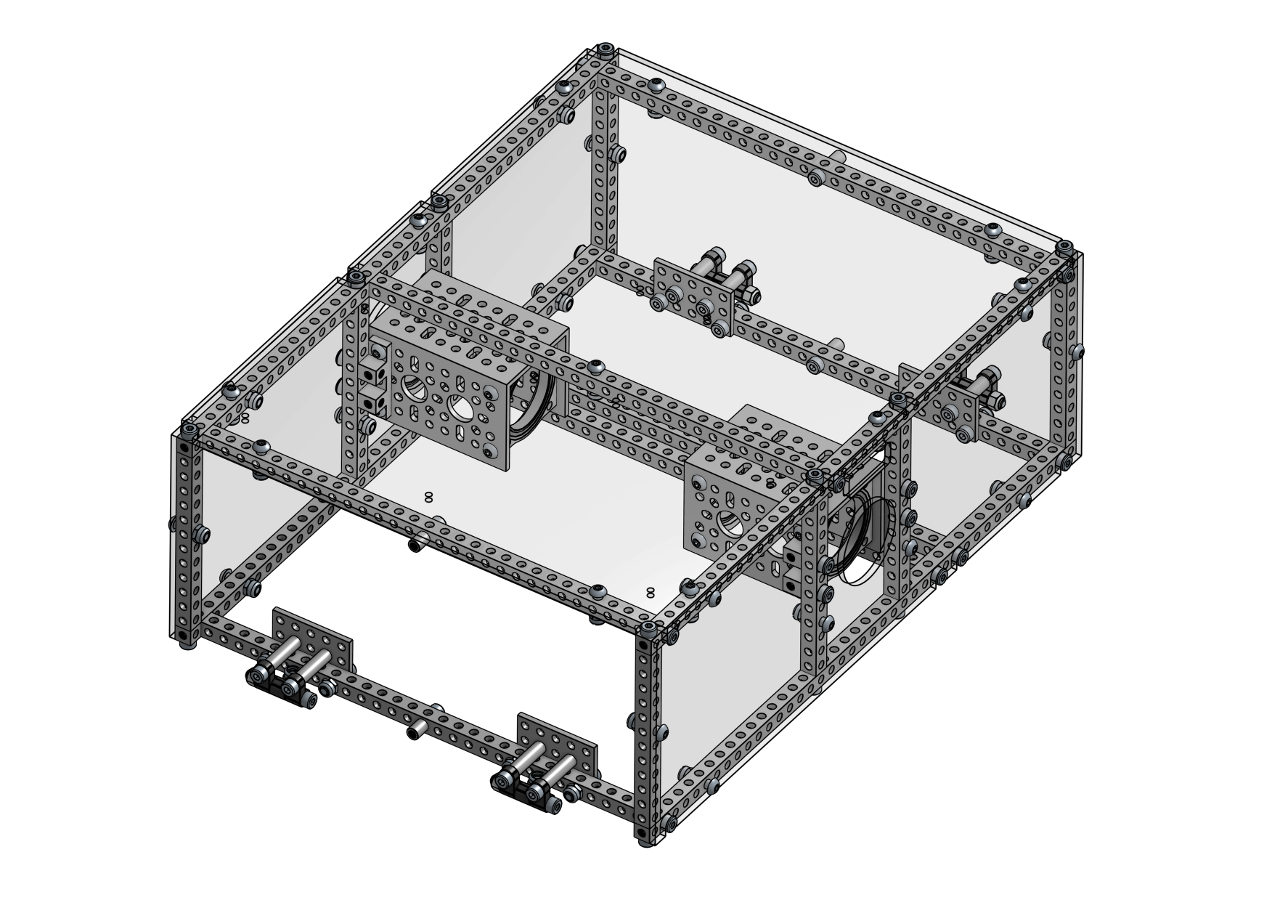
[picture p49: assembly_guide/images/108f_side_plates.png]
 

### 1.9 Front and Back Plates

#### Required Parts

| Amount | Part | Part Number | Link |
| :----: | --- | --- | ---- |
| 1 | Front Plate (lasercut) | front_plate.dxf | |
| 1 | Back Plate (lasercut) | back_plate.dxf  | |
| 4 | `M4 x 6mm` Button Head Screw  | | |
| 8 | `M4 x 16mm` Button Head Screw | | |
| 8 | `M4` Nylock Nut | | |

#### Assembly Info

> ⚠️ Pay attention to the orientation of the _Back Plate_!

Use 6mm screws to secure the plates to the standoffs.

> 🔃 The 3D model is upside down in the following image!

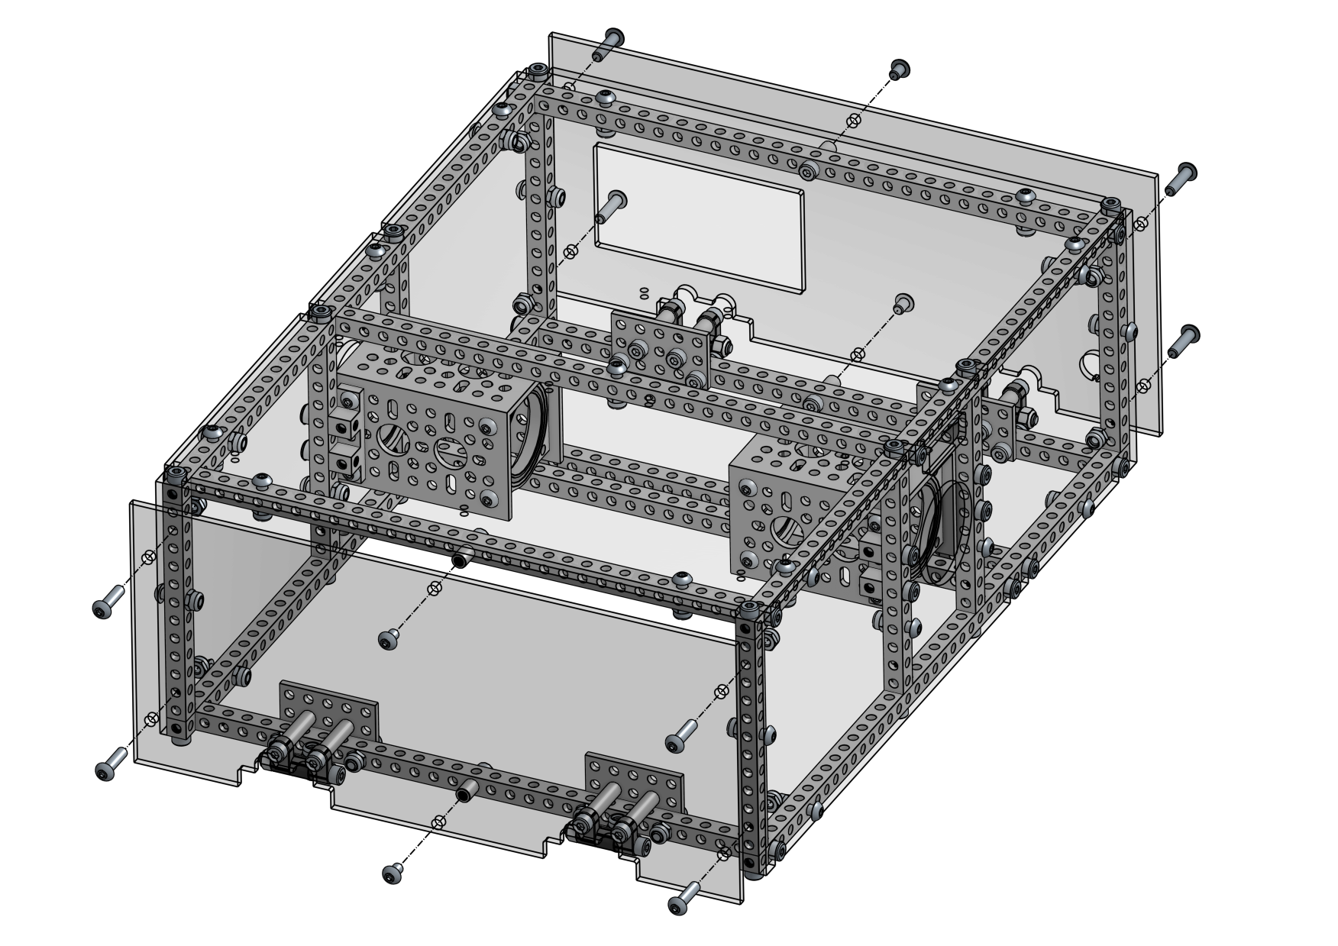
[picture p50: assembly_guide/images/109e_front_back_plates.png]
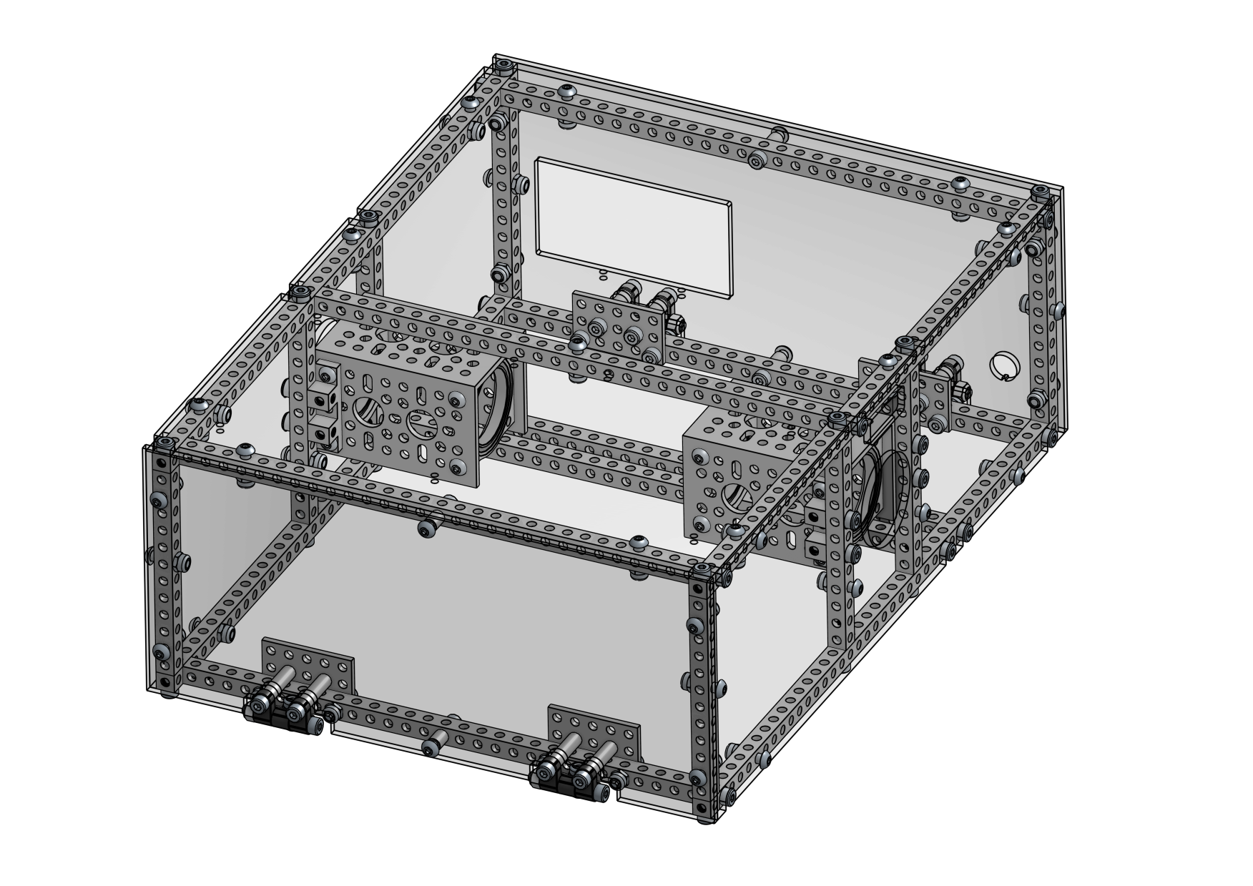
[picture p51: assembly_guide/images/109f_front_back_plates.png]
 

### 1.10 Top Plates

#### Required Parts

| Amount | Part | Part Number | Link |
| :----: | --- | --- | ---- |
| 1 | Top Plate Front (lasercut) | top_plate_front.dxf | |
| 1 | Top Plate Gap (lasercut) | top_plate_gap.dxf | |
| 1 | Top Plate Back (lasercut) | top_plate_back.dxf  | |
| 4 | `M4 x 10mm` Button Head Screw | | |
| 4 | `M4 x 16mm` Button Head Screw | | |
| 8 | `M4` Nylock Nut | | |

#### Assembly Info

Use the 10mm screws to secure the front and back top plates to the plastic hinges. Use the 16mm screws to mount the gap plate to the square beam between the other top plates.

> 💡 Tighten or loosen the screw inside the hinges to adjust the hinge tension. The top plates should open smoothly and stay in place when opened.

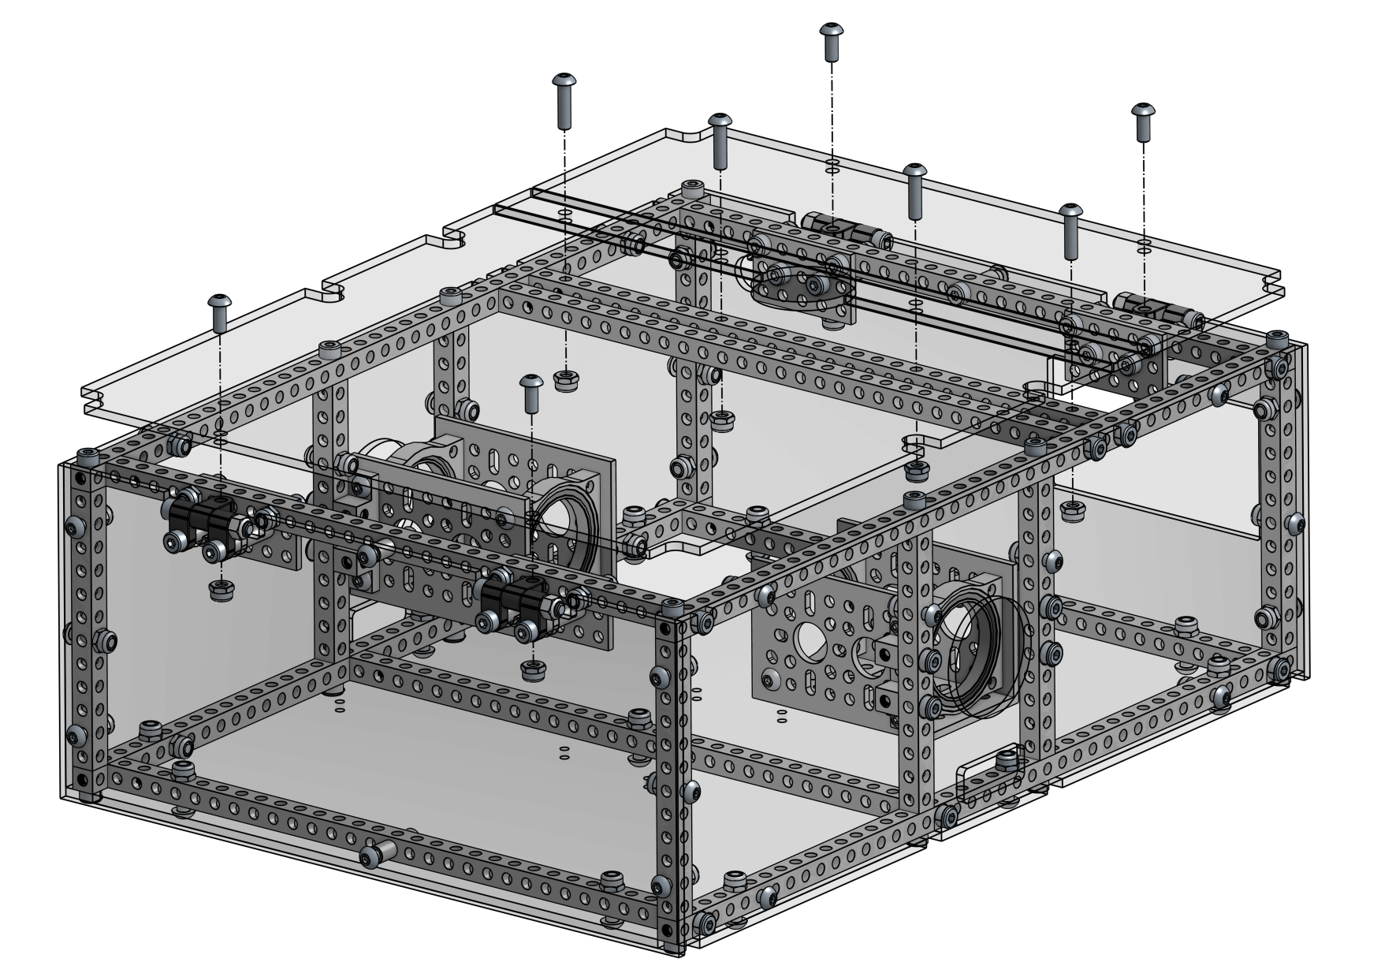
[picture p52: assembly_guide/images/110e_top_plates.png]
 

### 1.11 Differential Pivot

#### Required Parts

| Amount | Part | Part Number | Link |
| :----: | --- | --- | --- |
| 1 | Idler Bearing-Hub (**32mm OD**, **16mm Height**) | 1608-0001-0001 | https://www.gobilda.com/idler-bearing-hub-32mm-od-16mm-height/ |
| 1 | 1101 Series U-Beam (**41 Hole**, 328mm Length) | 1101-0041-0328 | https://www.gobilda.com/1101-series-u-beam-41-hole-328mm-length/ |
| 2 | `M4 x 6mm` Button Head Screw | | |
| 4 | `M4 x 16mm` Socket Head Screw | | |

#### Assembly Info

Secure the _U-Beam_ to the _Idler Bearing-Hub_ using the 6mm button head screws. Slide them into the _U-Beam_ through hole `20` and `22` and use an allen key to tighten them. Then mount the _Idler Bearing-Hub_ to the aluminum frame using the 16mm socket head screws.

 

### Next Steps

> 🎉 Congratulations on completing the main body assembly!

- [x] 1 Main Body
- [ ] [2 Wheels](2_wheels.md)
- [ ] [3 Rocker Bogie](3_rocker_bogie.md)
- [ ] [4 Final Steps](4_final_steps.md)

Continue with building the [Wheels](2_wheels.md)!

### Required Parts (Main Body)

This is a summary of all parts required in this chapter.

| Amount | Part | Part Number | Link |
| :----: | --- | --- | --- |
| 1 | 1101 Series U-Beam (**41 Hole**, 328mm Length) | 1101-0041-0328 | https://www.gobilda.com/1101-series-u-beam-41-hole-328mm-length/ |
| 8 | 1106 Series Square Beam (**12 Hole**, 96mm Length) | 1106-0012-0096 | https://www.gobilda.com/1106-series-square-beam-12-hole-96mm-length/ |
| 7 | 1106 Series Square Beam (**29 Hole**, 232mm Length) | 1106-0029-0232 | https://www.gobilda.com/1106-series-square-beam-29-hole-232mm-length/ |
| 4 | 1106 Series Square Beam (**41 Hole**, 328mm Length) | 1106-0041-0328 | https://www.gobilda.com/1106-series-square-beam-41-hole-328mm-length/ |
| 4 | 1116 Series Grid Plate (**3 x 5 Hole**, 24 x 40mm) | 1116-0024-0040 | https://www.gobilda.com/1116-series-grid-plate-3-x-5-hole-24-x-40mm/ |
| 2 | 1120 Series U-Channel (**2 Hole**, 72mm Length) | 1120-0002-0072 | https://www.gobilda.com/1120-series-u-channel-2-hole-72mm-length/ |
| 4 (2)  | 1205 Series Dual Block Mount (1-4) - 2 Pack | 1205-0001-0004 | https://www.gobilda.com/1205-series-dual-block-mount-1-4-2-pack/ |
| 4 (1)  | 1501 Series M4 x 0.7mm Standoff (**6mm OD**, **8mm Length**) - 4 Pack  | 1501-0006-0080 | https://www.gobilda.com/1501-series-m4-x-0-7mm-standoff-6mm-od-8mm-length-4-pack/  |
| 8 (2)  | 1501 Series M4 x 0.7mm Standoff (**6mm OD**, **22mm Length**) - 4 Pack | 1501-0006-0220 | https://www.gobilda.com/1501-series-m4-x-0-7mm-standoff-6mm-od-22mm-length-4-pack/ |
| 4 | **32mm** Bore 2-Side, 2-Post Pillow Block (**43mm Width**) | 1604-0043-0032 | https://www.gobilda.com/32mm-bore-2-side-2-post-pillow-block-43mm-width/ |
| 1 | Idler Bearing-Hub (**32mm OD**, **16mm Height**) | 1608-0001-0001 | https://www.gobilda.com/idler-bearing-hub-32mm-od-16mm-height/ |
| 4 (2)  | Plastic Hinge - 2 Pack | 2902-0003-0001 | https://www.gobilda.com/plastic-hinge-2-pack/ |
| 1 | Bottom Plate (lasercut) | bottom_plate.dxf | |
| 2 | Side Plate (lasercut) | side_plate.dxf | |
| 1 | Front Plate (lasercut) | front_plate.dxf | |
| 1 | Back Plate (lasercut) | back_plate.dxf | |
| 1 | Top Plate Front (lasercut) | top_plate_front.dxf | |
| 1 | Top Plate Gap (lasercut) | top_plate_gap.dxf | |
| 1 | Top Plate Back (lasercut) | top_plate_back.dxf  | |
| 14 | `M4 x 6mm` Button Head Screw | | |
| 12 | `M4 x 10mm` Button Head Screw | | |
| 39 | `M4 x 16mm` Button Head Screw | | |
| 20 | `M4 x 12mm` Socket Head Screw | | |
| 50 | `M4 x 16mm` Socket Head Screw | | |
| 51 | `M4` Nylock Nut | | |

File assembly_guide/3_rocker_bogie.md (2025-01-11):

# Mechanical Assembly Guide

## 3 Rocker Bogie



#### Assembly Steps

- 3.1 [Hinge Outer Part (4x)](#31-hinge-outer-part-4x)
- 3.2 [Hinge Inner Part (2x)](#32-hinge-inner-part-2x)
- 3.3 [Hinge Assembly (2x)](#33-hinge-assembly-2x)
- 3.4 [Servo Block (4x)](#34-servo-block-4x)
- 3.5 [Rear Servo Arm (L/R)](#35-rear-servo-arm-lr)
- 3.6 [Front Servo Arm (L/R)](#36-front-servo-arm-lr)
- 3.7 [Pivot Plate (L/R)](#37-pivot-plate-lr)
- 3.8 [Top Plate (L/R)](#38-top-plate-lr)
- 3.9 [Rocker Bogie Rear Assembly (L/R)](#39-rocker-bogie-rear-assembly-lr)
- 3.10 [Rocker Bogie Front Assembly (L/R)](#310-rocker-bogie-front-assembly-lr)
- [Required Parts (Rocker Bogie)](#required-parts-rocker-bogie)

### 3.1 Hinge Outer Part (4x)

#### Required Parts

| Amount | Part | Part Number | Link |
| :----: | --- | --- | --- |
| 4 | Plastic Hub-Mount Control Arm (**72mm Length**) | 1916-0014-0072 | https://www.gobilda.com/plastic-hub-mount-control-arm-72mm-length/ |
| 4 (2)  | 1114 Series Flat Bracket (**1-1**) - 2 Pack | 1114-0001-0001 | https://www.gobilda.com/1114-series-flat-bracket-1-1-2-pack/ |
| 4 | 1504 Series **32mm OD** Pattern Spacer (**2mm Length**) | 1504-0032-0020 | https://www.gobilda.com/1504-series-32mm-od-pattern-spacer-2mm-length/ |
| 4 (2)  | 1611 Series Flanged Ball Bearing (**8mm ID** x **14mm OD**, **5mm Thickness**) - 2 Pack | 1611-0514-0008 | https://www.gobilda.com/1611-series-flanged-ball-bearing-8mm-id-x-14mm-od-5mm-thickness-2-pack/ |
| 8 | Hurricane Nut for goRAIL | 2805-0004-0108 | |
| 16 | `M4 x 8mm` Socket Head Screw | | |
| 8 | `M4 x 12mm` Socket Head Screw | | |
| 24 | `M4 x 0.1mm` Washer | | |

#### Assembly Info

> ⚠️ Use washers between screw heads and plastic parts!

Insert the _Flanged Ball Bearing_ into the _Pattern Spacer_. Screw the _Control Arm_ to the _Pattern Spacer_ with the _Flanged Ball Bearing_ facing the _Control Arm_ using 8mm socket head screws. Install the _Flat Bracket_ to holes `3` and `7` of the _Control Arm_ so that the first two holes of the _Control Arms_ are not covered by the _Flat Bracket_. Use 12mm socket head screws and _Hurricane Nuts_ for this. The _Flat Bracket_ will stick out a bit.

 

### 3.2 Hinge Inner Part (2x)

#### Required Parts

| Amount | Part | Part Number | Link |
| :----: | --- | --- | --- |
| 2 | 1309 Series Sonic Hub (**8mm Bore**) | 1309-0016-0008 | https://www.gobilda.com/1309-series-sonic-hub-8mm-bore/ |
| 2 | **8mm** Shaft (Stainless Steel, **50mm Length**) | 2100-0008-0050 | https://www.gobilda.com/8mm-shaft-stainless-steel-50mm-length/ |
| 4 | 1221 Series 2-Side, 2-Post Pattern Mount (**32-2**) | 1221-0032-0002 | https://www.gobilda.com/1221-series-2-side-2-post-pattern-mount-32-2/ |
| 2 (1)  | 1522 Series 8mm ID Spacer (10mm OD, **6mm Length**) - 4 Pack | 1522-0010-0060 | https://www.gobilda.com/1522-series-8mm-id-spacer-10mm-od-6mm-length-4-pack/ |
| 2 (1)  | 1522 Series 8mm ID Spacer (10mm OD, **4mm Length**) - 4 Pack | 1522-0010-0040 | https://www.gobilda.com/1522-series-8mm-id-spacer-10mm-od-4mm-length-4-pack/ |
| 16 | `M4 x 6mm` Button Head Screw | | |

#### Assembly Info

Insert the shaft into the _Sonic Hub_ and tighten the _Sonic Hub_ in the center of the shaft. Screw the _Pattern Mounts_ to each side of the _Sonic Hub_ using 6mm button head screws. The flat side of the _Pattern Mounts_ must face towards the _Sonic Hub_.

> ⚠️ Pay attention to the two different spacer lengths!

Slide the _4mm Spacer_ onto the shaft on the side where the _Sonic Hub_ is slightly further out and the _6mm Spacer_ on the side where the _Sonic Hub_ is flat.

 

### 3.3 Hinge Assembly (2x)

#### Required Parts

| Amount | Part | Part Number | Link |
| :----: | --- | --- | --- |
| 4 | [Hinge Outer Part](#31-hinge-outer-part-4x) | | |
| 2 | [Hinge Inner Part](#32-hinge-inner-part-2x) | | |
| 2 | 1118 Series Open goRAIL (**96mm Length**) | 1118-0024-0096 | https://www.gobilda.com/1118-series-open-gorail-96mm-length/ |

#### Assembly Info

Slide one of the _Outer Parts_ onto either side of the _Inner Part_ with the _Hurricane Nuts_ facing inwards. Slide the _goRAIL_ into place until it is flush with the _Flat Bracket_ and tighten the screws.

> ⚠️ The open side of the _goRAIL_ must face towards one of the _Outer Parts_!

 

### 3.4 Servo Block (4x)

#### Required Parts

| Amount | Part | Part Number | Link |
| :----: | --- | --- | --- |
| 4 | ServoBlock® (Standard Size, 25 Tooth Spline, Hub-Shaft) | 3202-0001-2501 | https://www.gobilda.com/servoblock-standard-size-25-tooth-spline-hub-shaft/ |
| 4 | 2000 Series Dual Mode Servo (**25-2**, **Torque**) | 2000-0025-0002 | https://www.gobilda.com/2000-series-dual-mode-servo-25-2-torque/ |

#### Assembly Info

> 💡 Insert the _Servo_ first. Assemble the rest of the _Servo Block_ loosely. Attach the shaft to the servo first before tightening all the screws.

> ⚠️ Secure the shaft to the servo with the M3 screw included with the servo!

 

### 3.5 Rear Servo Arm (L/R)

#### Required Parts

| Amount | Part | Part Number | Link |
| :----: | --- | --- | --- |
| 2 | 1118 Series Open goRAIL (**288mm Length**) | 1118-0024-0288 | https://www.gobilda.com/1118-series-open-gorail-288mm-length/ |
| 2 | 1120 Series U-Channel (**1 Hole**, 48mm Length) | 1120-0001-0048 | https://www.gobilda.com/1120-series-u-channel-1-hole-48mm-length/ |
| 2 | [Servo Block](#34-servo-block-4x) | | |
| 16 | `M4 x 8mm` Socket Head Screw | | |
| 8 | `M4 x 12mm` Socket Head Screw | | |

#### Assembly Info

Screw the _U-Channel_ to the _goRAIL_ first using 12mm socket head screws, before installing the _Servo Block_ with 8mm socket head screws.

#### 3.5.1 Left Rear Servo Arm

> ⚠️ The open side of the _goRAIL_ faces to the right side when looking from the _Servo Block_ (away from the camera in the following image).

 

#### 3.5.2 Right Rear Servo Arm

> ⚠️ The open side of the _goRAIL_ faces to the left side when looking from the _Servo Block_ (away from the camera in the following image).

 

### 3.6 Front Servo Arm (L/R)

#### Required Parts

| Amount | Part | Part Number | Link |
| :----: | --- | --- | --- |
| 2 | 1118 Series Open goRAIL (**96mm Length**) | 1118-0024-0096 | https://www.gobilda.com/1118-series-open-gorail-96mm-length/ |
| 2 | 1111 Series Angle Pattern Bracket (**3-1**) | 1111-0003-0001 | https://www.gobilda.com/1111-series-angle-pattern-bracket-3-1/ |
| 2 | 1116 Series Grid Plate (**3 x 5 Hole**, 24 x 40mm) | 1116-0024-0040 | https://www.gobilda.com/1116-series-grid-plate-3-x-5-hole-24-x-40mm/ |
| 2 | [Servo Block](#34-servo-block-4x) | | |
| 16 | `M4 x 8mm` Socket Head Screw | | |
| 16 | `M4 x 12mm` Socket Head Screw | | |

#### Assembly Info

Screw the _U-Channel_ and _Grid Plate_ to the _goRAIL_ first using 12mm socket head screws.

> ⚠️ Make sure to install the _3 x 5 Grid Plate_ in the correct orientation. It should stick out at the top and bottom, not to the sides.

Install the _Servo Block_ with 8mm socket head screws. The cable should point towards the _goRAIL_. The _Servo Block_ is supposed to stick out of the _U-Channel_.

#### 3.6.1 Left Front Servo Arm

> ⚠️ The open side of the _goRAIL_ faces to the left, when looking from the _Servo Block_ (away from the camera in the following image).

 

#### 3.6.2 Right Front Servo Arm

> ⚠️ The open side of the _goRAIL_ faces to the right, when looking from the _Servo Block_ (away from the camera in the following image).

 

### 3.7 Pivot Plate (L/R)

#### Required Parts

| Amount | Part | Part Number | Link |
| :----: | --- | --- | --- |
| 2 | 1111 Series Angle Pattern Bracket (**1-1**) | 1111-0001-0001 | https://www.gobilda.com/1111-series-angle-pattern-bracket-1-1/ |
| 4 (1)  | 1203 Series Block Mount (1-1) - 4 Pack | 1203-0001-0001 | https://www.gobilda.com/1203-series-block-mount-1-1-4-pack/ |
| 4 (2)  | 1102 Series Flat Beam (**7 Hole**, 56mm Length) - 2 Pack | 1102-0007-0056 | https://www.gobilda.com/1102-series-flat-beam-7-hole-56mm-length-2-pack/ |
| 4 (2)  | 2913 Series Steel Ball Linkage (**Female** M4 x 0.7mm, 24.1mm Length) - 2 Pack  | 2913-0004-0241 | https://www.gobilda.com/2913-series-steel-ball-linkage-female-m4-x-0-7mm-24-1mm-length-2-pack/  |
| 2 (1)  | 2808 Series Stainless Steel Threaded Rod (M4 x 0.7mm, **50mm Length**) - 2 Pack | 2808-0004-0050 | https://www.gobilda.com/2808-series-stainless-steel-threaded-rod-m4-x-0-7mm-50mm-length-2-pack/ |
| 4 | `M4 x 8mm` Socket Head Screw | | |
| 4 | `M4 x 12mm` Socket Head Screw | | |
| 2 | `M4 x 20mm` Socket Head Screw | | |
| 2 | `M4` Nylock Nut | | |

#### Assembly Info

Install the _Block Mounts_ using 8mm socket head screws with the chamfered edge facing the edge of the _Angle Pattern Bracket_. Do not tighten the screws completely. Use 12mm socket head screws to loosely attach one _Flat Beam_ to each _Block Mount_ on opposite sides. Screw _Steel Ball Linkages_ to both ends of the _Threaded Rod_ until they are about 26mm apart and one is turned 90 degrees. Slide the _Steel Ball Linkage_ between the two _Flat Beams_ and secure it using a 20mm socket head screw and a Nylock nut. Tighten all screws now.

> ⚠️ When all screws are tightened, the _Block Mounts_ will be at a slight angle. This is expected behavior.

#### 3.7.1 Left Pivot Plate

 

#### 2.7.2 Right Pivot Plate

 

### 3.8 Top Plate (L/R)

#### Required Parts

| Amount | Part | Part Number | Link |
| :----: | --- | --- | --- |
| 2 | [Pivot Plate (L/R)](#37-pivot-plate-lr) | | |
| 2 (1)  | 1137 Series Steel Flat Grid Bracket (1-1) - 2 Pack | 1137-0001-0001 | https://www.gobilda.com/1137-series-steel-flat-grid-bracket-1-1-2-pack/ |
| 16 | Hurricane Nut for goRAIL | 2805-0004-0108 | |
| 10 | `M4 x 6mm` Button Head Screw | | |
| 6 | `M4 x 8mm` Socket Head Screw | | |

#### Assembly Info

Insert three 6mm button head screws into the ends of the _Grid Bracket_ as shown in the pictures. Loosely fit _Hurricane Nuts_ on the other side. Attach the _Grid Bracket_ to the underside of the _Angle Pattern Bracket_ so that the button head screws and half a hole protrude. Secure it in place with three 8mm socket head screws and slightly loose _Hurricane Nuts_ as seen in the pictures. Add two 6mm screws and _Hurricane Nuts_ to the angled side of the _Angle Pattern Bracket_.

> ⚠️ The _Hurricane Nuts_ should form two perpendicular lines. One line of five across the fold and a line of three parallel to the fold between the _Flat Brackets_.

#### 3.8.1 Left Top Plate

 

#### 3.8.2 Right Top Plate

 

### 3.9 Rocker Bogie Rear Assembly (L/R)

#### Required Parts

| Amount | Part | Part Number | Link |
| :----: | --- | --- | --- |
| 2 | [Top Plate (L/R)](#37-pivot-plate-lr) | | |
| 2 | [Rear Servo Arm (L/R)](#35-rear-servo-arm-lr) | | |
| 2 | [Hinge Assembly](#33-hinge-assembly-2x) | | |
| 2 | 1111 Series Angle Pattern Bracket (**1-1**) | 1111-0001-0001 | https://www.gobilda.com/1111-series-angle-pattern-bracket-1-1/ |
| 2 | 1118 Series Open goRAIL (**120mm Length**) | 1118-0024-0120 | https://www.gobilda.com/1118-series-open-gorail-120mm-length/ |
| 4 (2)  | 1506 Series 32mm ID Spacer (36mm OD, **6mm Length**) - 2 Pack | 1506-0032-0006 | https://www.gobilda.com/1506-series-32mm-id-spacer-36mm-od-6mm-length-2-pack/ |
| 8 | Hurricane Nut for goRAIL | 2805-0004-0108 | |
| 8 | `M4 x 6mm` Button Head Screw | | |

#### Assembly Info

Insert four 6mm button head screws into the new _Angle Pattern Bracket_ in the same holes as the _Top Plate_ assembly and loosely secure them with _Hurricane Nuts_.

> ⚠️ The open side of the _goRAILs_ in the _Hinge Assembly_ and _Rear Servo Arms_ should face towards the center of the _Anlge Pattern Bracket_ and the _Steel Ball Bearing_!

Slide the _Rear Servo Arm_ onto the new _Angle Pattern Bracket_ up to the fold and tighten the screws. Slide the _Top Plate_ into the _Rear Servo Arm_ as well, but leave it loose for now. Insert the _Hinge Assembly_ into both _Angle Pattern Brackets_ up to the fold of the bottom one. Tighten the bottom screws. Now insert the _120mm goRAIL_ between the _Angle Pattern Brackets_ below the pivot point up to the _Rear Servo Arm_.

> ⚠️ The open side of the _120mm goRAIL_ should face sideways towards the _Hinge Assembly_!

Once all _goRAILs_ are in place, tighten all remaining screws and slide two spacer rings onto the _120mm goRAIL_.

#### 3.9.1 Left Rear Assembly

 

#### 3.9.2 Right Rear Assembly

 

### 3.10 Rocker Bogie Front Assembly (L/R)

#### Required Parts

| Amount | Part | Part Number | Link |
| :----: | --- | --- | --- |
| 2 | [Front Servo Arm (L/R)](#36-front-servo-arm-lr) | | |
| 2 | [Middle Wheel (L/R)](2_wheels.md#22-middle-wheels-lr) | | |
| 8 (4)  | 1102 Series Flat Beam (**3 Hole**, 24mm Length) - 2 Pack | 1102-0003-0024 | https://www.gobilda.com/1102-series-flat-beam-3-hole-24mm-length-2-pack/ |
| 16 | `M4 x 12mm` Socket Head Screw | | |

#### Assembly Info

Attach the _Front Servo Arm_ and _Middle Wheel_ to the hinge using 12mm socket head screws and _Flat Beams_ as spacers in between.

> ⚠️ Make sure the open sides of all _goRAILs_ face the same direction, where the main body is going.

#### 3.10.1 Left Front Assembly

 

#### 3.10.2 Right Front Assembly

 

### Next Steps

> 🎉 Congratulations on completing the rocker bogie assembly!

- [x] [1 Main Body](1_main_body.md)
- [x] [2 Wheels](2_wheels.md)
- [x] 3 Rocker Bogie
- [ ] [4 Final Steps](4_final_steps.md)

Continue with the [Final Steps](4_final_steps.md) to put it all together!

### Required Parts (Rocker Bogie)

This is a summary of all parts required in this chapter.

| Amount | Part | Part Number | Link |
| :----: | --- | --- | --- |
| 8 (4)  | 1102 Series Flat Beam (**3 Hole**, 24mm Length) - 2 Pack | 1102-0003-0024 | https://www.gobilda.com/1102-series-flat-beam-3-hole-24mm-length-2-pack/ |
| 4 (2)  | 1102 Series Flat Beam (**7 Hole**, 56mm Length) - 2 Pack | 1102-0007-0056 | https://www.gobilda.com/1102-series-flat-beam-7-hole-56mm-length-2-pack/ |
| 4 | 1111 Series Angle Pattern Bracket (**1-1**) | 1111-0001-0001 | https://www.gobilda.com/1111-series-angle-pattern-bracket-1-1/ |
| 2 | 1111 Series Angle Pattern Bracket (**3-1**) | 1111-0003-0001 | https://www.gobilda.com/1111-series-angle-pattern-bracket-3-1/ |
| 4 (2)  | 1114 Series Flat Bracket (**1-1**) - 2 Pack | 1114-0001-0001 | https://www.gobilda.com/1114-series-flat-bracket-1-1-2-pack/ |
| 2 | 1116 Series Grid Plate (**3 x 5 Hole**, 24 x 40mm) | 1116-0024-0040 | https://www.gobilda.com/1116-series-grid-plate-3-x-5-hole-24-x-40mm/ |
| 4 | 1118 Series Open goRAIL (**96mm Length**) | 1118-0024-0096 | https://www.gobilda.com/1118-series-open-gorail-96mm-length/ |
| 2 | 1118 Series Open goRAIL (**288mm Length**) | 1118-0024-0288 | https://www.gobilda.com/1118-series-open-gorail-288mm-length/ |
| 2 | 1118 Series Open goRAIL (**120mm Length**) | 1118-0024-0120 | https://www.gobilda.com/1118-series-open-gorail-120mm-length/ |
| 2 | 1120 Series U-Channel (**1 Hole**, 48mm Length) | 1120-0001-0048 | https://www.gobilda.com/1120-series-u-channel-1-hole-48mm-length/ |
| 2 (1)  | 1137 Series Steel Flat Grid Bracket (1-1) - 2 Pack | 1137-0001-0001 | https://www.gobilda.com/1137-series-steel-flat-grid-bracket-1-1-2-pack/ |
| 4 (1)  | 1203 Series Block Mount (1-1) - 4 Pack | 1203-0001-0001 | https://www.gobilda.com/1203-series-block-mount-1-1-4-pack/ |
| 4 | 1221 Series 2-Side, 2-Post Pattern Mount (**32-2**) | 1221-0032-0002 | https://www.gobilda.com/1221-series-2-side-2-post-pattern-mount-32-2/ |
| 2 | 1309 Series Sonic Hub (**8mm Bore**) | 1309-0016-0008 | https://www.gobilda.com/1309-series-sonic-hub-8mm-bore/ |
| 4 | 1504 Series **32mm OD** Pattern Spacer (**2mm Length**) | 1504-0032-0020 | https://www.gobilda.com/1504-series-32mm-od-pattern-spacer-2mm-length/ |
| 4 (2)  | 1506 Series 32mm ID Spacer (36mm OD, **6mm Length**) - 2 Pack | 1506-0032-0006 | https://www.gobilda.com/1506-series-32mm-id-spacer-36mm-od-6mm-length-2-pack/ |
| 2 (1)  | 1522 Series 8mm ID Spacer (10mm OD, **4mm Length**) - 4 Pack | 1522-0010-0040 | https://www.gobilda.com/1522-series-8mm-id-spacer-10mm-od-4mm-length-4-pack/ |
| 2 (1)  | 1522 Series 8mm ID Spacer (10mm OD, **6mm Length**) - 4 Pack | 1522-0010-0060 | https://www.gobilda.com/1522-series-8mm-id-spacer-10mm-od-6mm-length-4-pack/ |
| 4 (2)  | 1611 Series Flanged Ball Bearing (**8mm ID** x **14mm OD**, **5mm Thickness**) - 2 Pack | 1611-0514-0008 | https://www.gobilda.com/1611-series-flanged-ball-bearing-8mm-id-x-14mm-od-5mm-thickness-2-pack/ |
| 4 | Plastic Hub-Mount Control Arm (**72mm Length**) | 1916-0014-0072 | https://www.gobilda.com/plastic-hub-mount-control-arm-72mm-length/ |
| 4 | 2000 Series Dual Mode Servo (**25-2**, **Torque**) | 2000-0025-0002 | https://www.gobilda.com/2000-series-dual-mode-servo-25-2-torque/ |
| 2 | **8mm** Shaft (Stainless Steel, **50mm Length**) | 2100-0008-0050 | https://www.gobilda.com/8mm-shaft-stainless-steel-50mm-length/ |
| 32 (2) | Hurricane Nut for goRAIL - 25 Pack | 2805-0004-0108 | https://www.gobilda.com/hurricane-nut-for-gorail-25-pack/ |
| 2 (1)  | 2808 Series Stainless Steel Threaded Rod (M4 x 0.7mm, **50mm Length**) - 2 Pack | 2808-0004-0050 | https://www.gobilda.com/2808-series-stainless-steel-threaded-rod-m4-x-0-7mm-50mm-length-2-pack/ |
| 4 (2)  | 2913 Series Steel Ball Linkage (**Female** M4 x 0.7mm, 24.1mm Length) - 2 Pack | 2913-0004-0241 | https://www.gobilda.com/2913-series-steel-ball-linkage-female-m4-x-0-7mm-24-1mm-length-2-pack/  |
| 4 | ServoBlock® (Standard Size, 25 Tooth Spline, Hub-Shaft) | 3202-0001-2501 | https://www.gobilda.com/servoblock-standard-size-25-tooth-spline-hub-shaft/ |
| 34 | `M4 x 6mm` Button Head Screw | | |
| 58 | `M4 x 8mm` Socket Head Screw | | |
| 52 | `M4 x 12mm` Socket Head Screw | | |
| 2 | `M4 x 20mm` Socket Head Screw | | |
| 2 | `M4` Nylock Nut | | |
| 24 | `M4 x 0.1mm` Washer | | |

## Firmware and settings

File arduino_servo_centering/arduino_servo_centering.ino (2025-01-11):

#include <Servo.h>

/*
  How to connect your servo:

  1. Connect the red wire (VCC) of the servo to the 5V pin on the Arduino.
  2. Connect the black wire (GND) of the servo to one of the GND pins on the Arduino.
  3. Connect the white wire (signal) of the servo to pin 9 on the Arduino.

  Make sure you have a stable power source, as the servo may draw more current than the Arduino can provide through its 5V pin alone.
*/

Servo myservo;

void setup()
{
    // Attach the servo to pin 9 on the Arduino
    myservo.attach(9);

    // Set the servo to its center position (90 degrees)
    myservo.write(90);
}

void loop()
{
    // Nothing needs to be done in the loop
}

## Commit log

2025-01-11 Mechanical Init
    [back_plate.dxf, bottom_plate.dxf, front_plate.dxf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]
2025-01-11 fixed arduino sketch reference
2025-01-11 enlarge assembly images
2025-01-11 remove markdown formatting in csv parts list
    [part_list.csv]
